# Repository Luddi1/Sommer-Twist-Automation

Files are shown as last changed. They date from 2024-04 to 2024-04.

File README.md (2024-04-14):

# Sommer Twist Automation
 Add-On PCB and ESPHome software to read gate state of Sommer twist 200 (and similar) to implement open and close commands

**Problem**:  Sommer Twist 200 (and similar) gate controllers only have an impulse-input. When toggling this input an open gate closes, closed gate opens and a moving gate stops. 
However, to integrate this into a smarter setup, distinct commands for _open_ and _close_ are needed. 

**Solution**: We read out the LEDs on the gate controller PCB which indicate whether the gate opens or closes, save the state and toggle the impulse-input, depending on the current state and the desired command. 

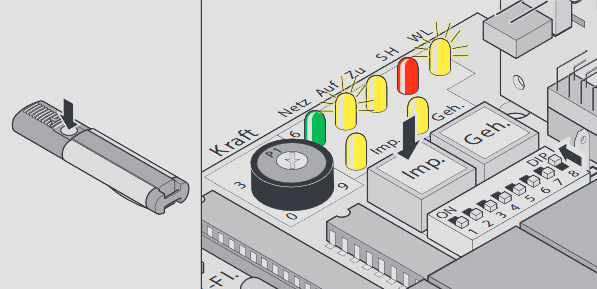
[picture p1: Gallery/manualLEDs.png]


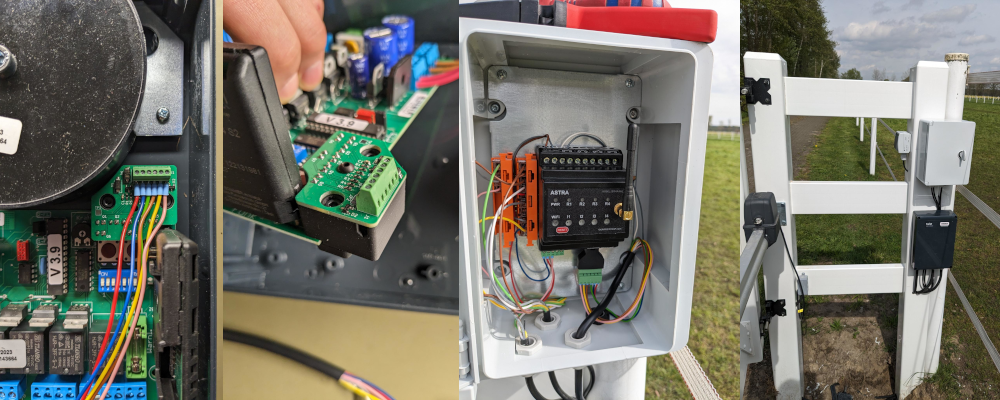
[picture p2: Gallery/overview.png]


This solution needs no hardware hacks on the original Sommer controller. 
Find below the contents of the repository, BOMs for the read-out PCB and the overall system. 

## Contents of repository
* **SommerAdapter** KiCad Project of PCB. Basically implements opto-couplers using the LEDs on the Sommer gate controller. 
* **SommerAdapter-Mount** Fusion 360 Project and step files to mount PCB on Sommer controller. 
* **Setup** ESPHome YAML Script for ASTRA controller and wiring diagram. 
* **Gallery** Some pictures of the installation. 

## BOM SommerAdapter PCB Assembly

Parts for one PCB of SommerAdapter/SommerAdapter.kicad_pcb

Component Refs | Value      | Package | Qty | Reichelt #
-------------- | ---------- | ------- | :-: | ------------
C1 |	100n |	C_0603_1608Metric |	1 | KEM Y5V0603 100N 
R1, R2, R3, R4, R5, R6, R7 |	47k |	R_0603_1608Metric |	7 | SMD-0603 47K
D2, D7 |	PESD3V3S2UT | 	SOT-23 |	2 | PESD3V3S2UT 
D1 |	SS 16 |	D_SMA |	1 | SS 16 
D6 |	P4SMAJ5.0CA |	D_SMA |	1 | P4SMAJ5.0CA 
Q1, Q2, Q3, Q4, Q5, Q6, Q7 |	SFH309-5 |	LED_D3.0mm_Clear |	7 | SFH 309-5 OSO 
J1 |	DG308 | 2,54-6 | 1 | DG308 2,54-6 

## BOM Complete Setup

For presented setup to control a Twist 200. Of course you can make use of the PCB with some other microcontroller and software in your own setup. 

Component | Qty
-------------- | ---------- 
SommerAdapter PCB Assembly |	1
3D printed SommerAdapter-Mount/LowerPart.step  |	1
3D printed SommerAdapter-Mount/UpperPart.step  |	1
ASTRA controller, 4 Relays 16A, 4 AC Input, AC power, LED (BR4A4AL)  |	1
RJ12 6P6C adapter with screw terminals |	1
Panhead screw M3 x 10 |	1
Socket head screw M3 x 16 | 2
Lapp 1030243 LiYY PVC Control Cable 8 x 0.34 mm² |	~2m
Distribiution box 180x240x130mm IP65 F-ELEKTRO 5901087041915 |	1
Momentary switch Aquant 1207-65 IP65 |	1
DIN rail, mounting hardware, some Wago 221 and DIN rail adapter 221-500, 0.34 ferrules  | 

Some notes:
* The printed parts are designed for ABS. Other materials will probably work, too. 
* Keep the cable run for the SommerAdapter PCB as short as possible and avoid runs next to other cables. 
* Flash ESPHome to ASTRA controller and set to SPI mode. See [manual](https://templates.blakadder.com/assets/ASTRA_controller.pdf). Use SPI (left) RJ12 socket. We need the GPIOs and GND/3.3V to power our board.

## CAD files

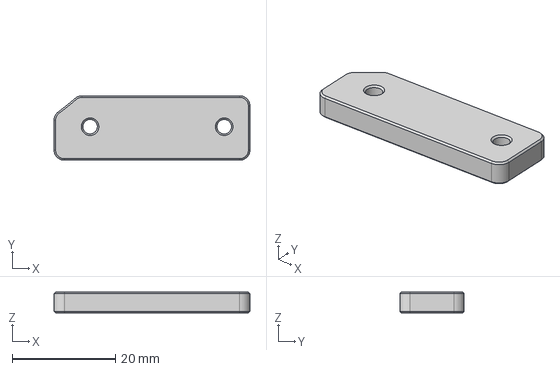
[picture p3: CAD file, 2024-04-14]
SommerAdapter-Mount/LowerPart.step
38.0 x 12.5 x 4.00 mm

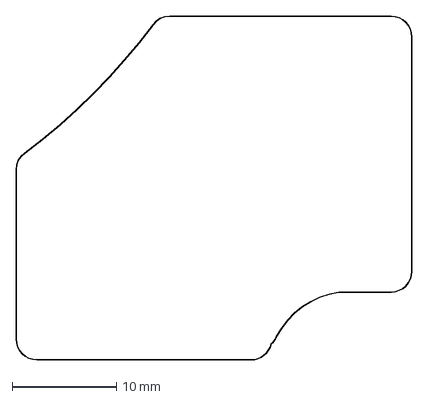
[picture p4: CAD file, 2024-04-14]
SommerAdapter/outline.dxf
38.0 x 33.0 mm

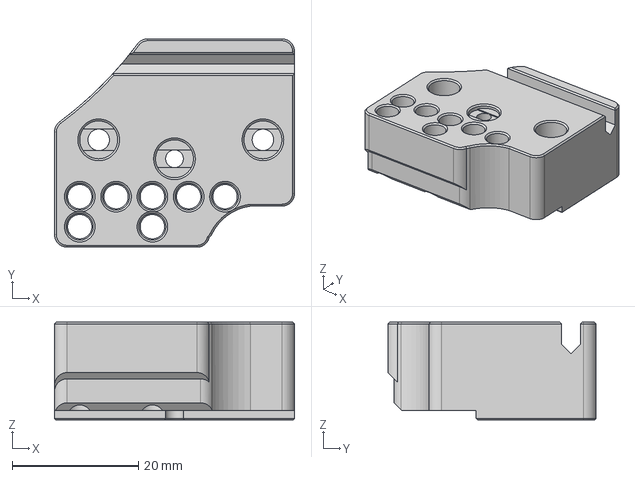
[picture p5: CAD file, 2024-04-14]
SommerAdapter-Mount/UpperPart.step
38.0 x 33.0 x 15.5 mm

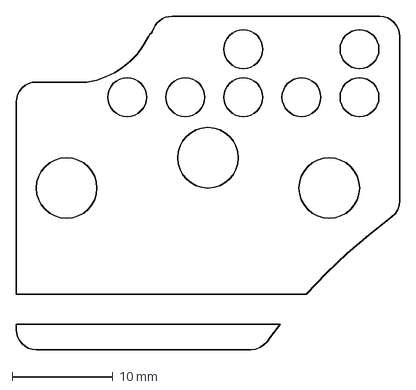
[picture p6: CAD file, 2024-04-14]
SommerAdapter/allfeatures.dxf
38.0 x 33.0 mm

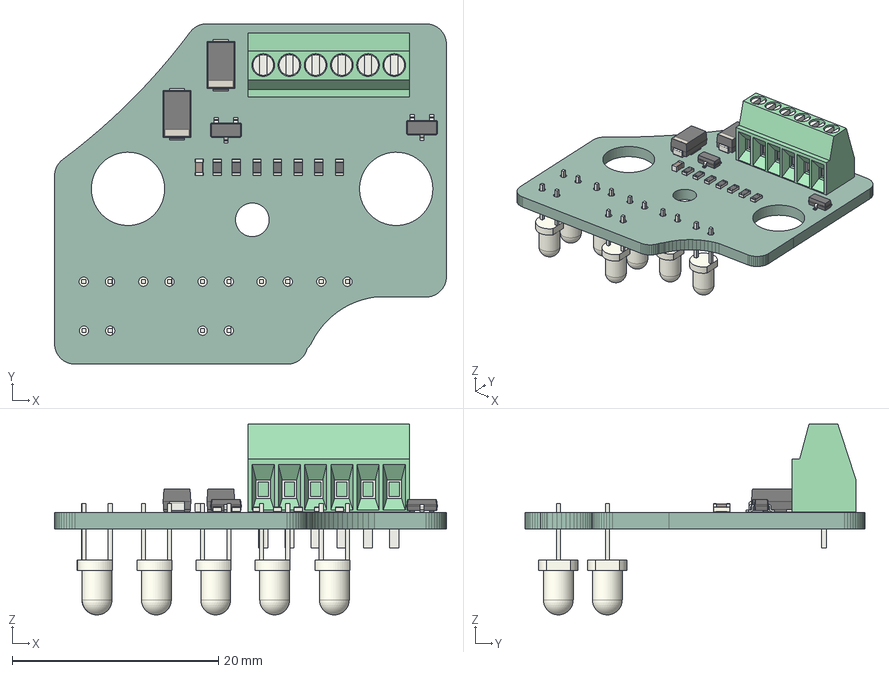
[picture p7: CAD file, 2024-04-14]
SommerAdapter/SommerAdapter.step
38.0 x 33.0 x 18.5 mm
C_0603_1608Metric
R_0603_1608Metric x 7
D_SMA x 2
SOT_23 x 2
TerminalBlock_Phoenix_MPT_05_6_254_1x06_P254mm_Horizontal
LED_D3.0mm_Clear x 7
SommerAdapter PCB

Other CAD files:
SommerAdapter-Mount/SommerAdapter-Mount.f3z

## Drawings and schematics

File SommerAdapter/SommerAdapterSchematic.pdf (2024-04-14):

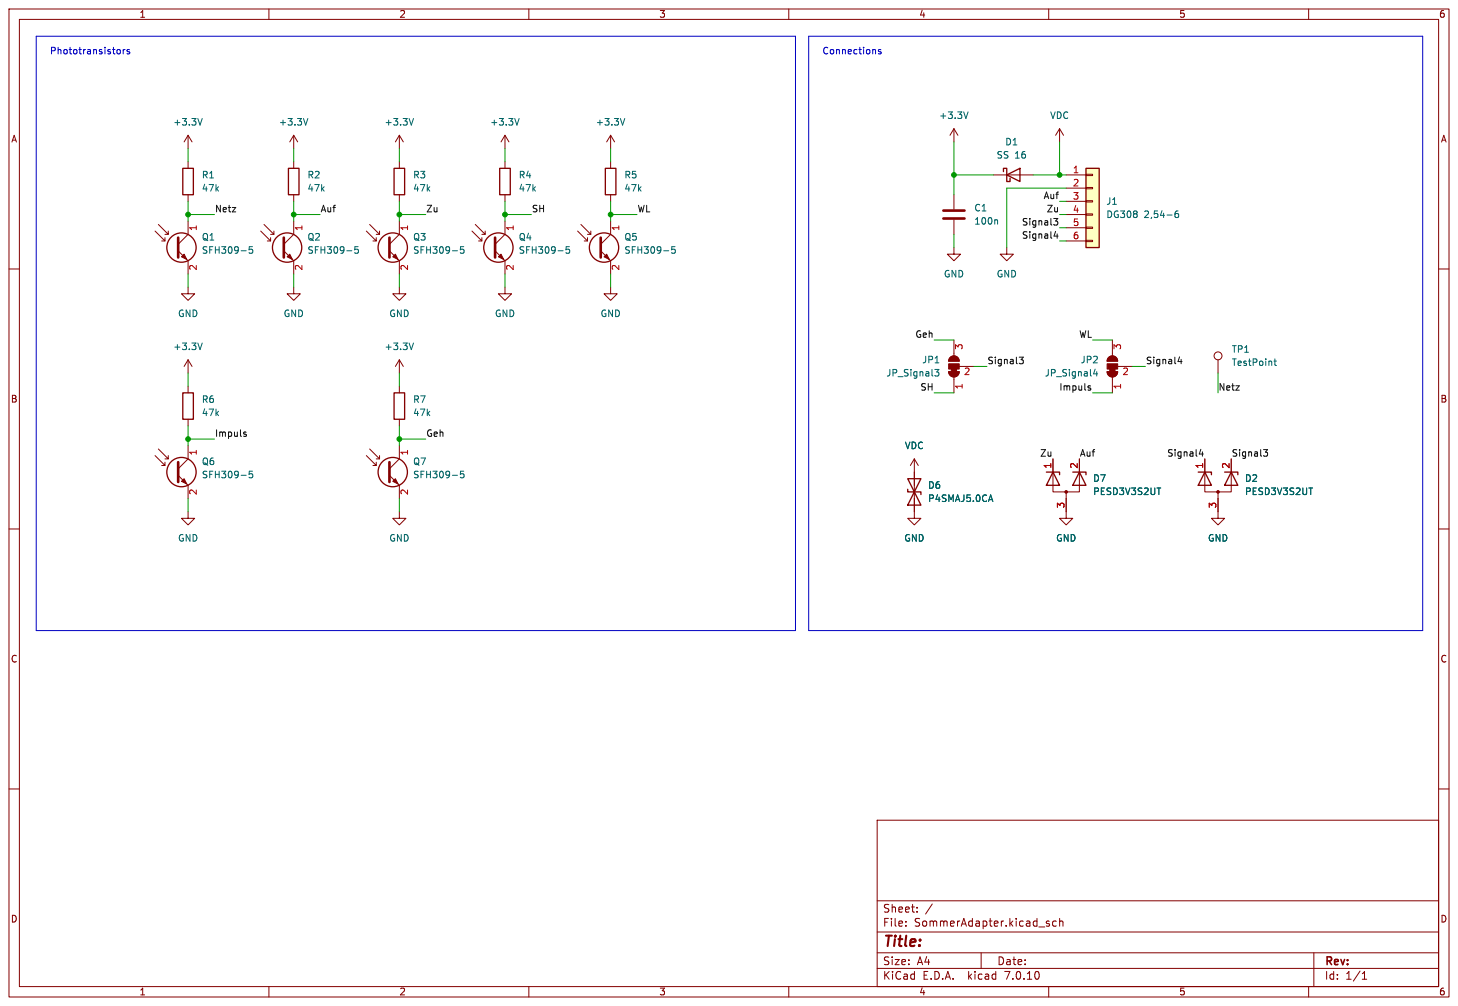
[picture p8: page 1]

Id: 1/1 Title: File: SommerAdapter.kicad_sch Sheet: / GND

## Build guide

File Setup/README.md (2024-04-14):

### Wiring diagram
of SommerAdapter only
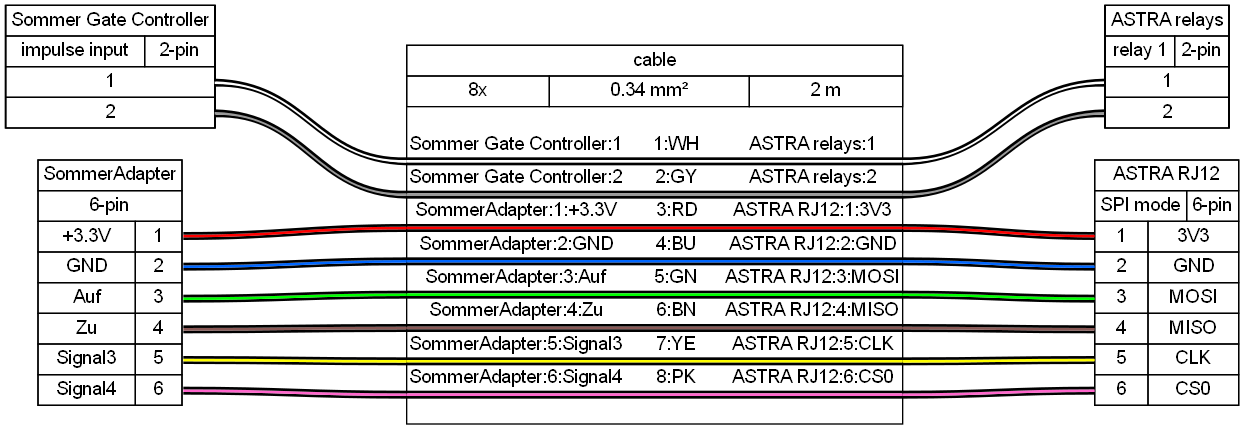
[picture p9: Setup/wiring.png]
Wiring diagram


In the presented setup ASTRA AC input 1 is connected to an induction looop, which triggers when a vehicle approaches. AC input 2 is connected to a momentary switch positioned at the gate. 

### ESPHome setup
ESPhome YAML file: astra-gate.yaml

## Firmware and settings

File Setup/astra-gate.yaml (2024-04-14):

esphome:
  name: astra-gate
  friendly_name: ASTRA-gate
  on_boot:
  # buzzeron on startup
    priority: -100
    then:
      - rtttl.play: 'BarbieGirl:d=4,o=5,b=125:8g#,8e,8g#,8c#6,a'

esp32:
  board: esp32dev
  framework:
    type: arduino

# Enable logging
logger:

ota:
  password: "4231c5ddbc304e2fb4416c7ab1234567"

wifi:
  ssid: !secret wifi_ssid
  password: !secret wifi_password
  reboot_timeout: 15min

  # Enable fallback hotspot (captive portal) in case wifi connection fails
  ap:
    ssid: "Astra-Gate Fallback Hotspot"
    password: "dYCe31234567"

captive_portal:
    
mqtt:
  broker: tower
  topic_prefix: "leusmann/gate"
  reboot_timeout: 15min
  on_message:
    - topic: leusmann/gate
      qos: 0
      then: # logic to open or close depending on current state
        - if:
            condition:
              and:
                - lambda: 'return x == "open";'
                - state_machine.state: "CLOSED"
            then:
              - logger.log: "mqtt -> Is closed, opening"
              - script.execute: open_close_script
        - if:
            condition:
              and:
                - lambda: 'return x == "open";'
                - state_machine.state: "CLOSING"
            then:
              - logger.log: "mqtt -> Is closing, stopping and opening"
              - script.execute: stop_reverse_script
        - if:
            condition:
              and:
                - lambda: 'return x == "close";'
                - state_machine.state: "OPEN"
            then:
              - logger.log: "mqtt -> Is open, closing"
              - script.execute: open_close_script
        - if:
            condition:
              and:
                - lambda: 'return x == "close";'
                - state_machine.state: "OPENING"
            then:
              - logger.log: "mqtt -> Is opening, stopping and closing"
              - script.execute: stop_reverse_script

external_components:
  - source:
      type: git
      url: https://github.com/muxa/esphome-state-machine

status_led:
  pin:
    number: GPIO4
    inverted: true

rtttl:
  output: rtttl_out

# Scripts for actions
script:
  - id: open_close_script
    then:
      - logger.log: "Running open_close_script"
      - output.turn_on: relay1
      - delay: 0.5s
      - output.turn_off: relay1
  - id: stop_reverse_script
    then:
      - logger.log: "Running stop_reverse_script"
      - output.turn_on: relay1
      - delay: 0.5s
      - output.turn_off: relay1
      - delay: 3.0s
      - output.turn_on: relay1
      - delay: 0.5s
      - output.turn_off: relay1

output:
  - platform: ledc
    pin: GPIO12
    id: rtttl_out
  - platform: gpio
    pin: 25
    id: relay1 # triggering gate controller
  - platform: gpio
    pin: 26
    id: relay2 # unused
  - platform: gpio
    pin: 33
    id: relay3 # unused
  - platform: gpio
    pin: 32
    id: relay4 # unused

binary_sensor:
  - platform: gpio
    name: "SWITCH 1" # signal from dual induction loop, triggered only when vehicle approaching
    pin: 
      number: 34
      inverted: true
      mode:
        input: true
    on_press: 
      if:
        condition:
          state_machine.state: "CLOSED"
        then:
          - logger.log: "Induction loop triggered -> Is closed, opening"
          - script.execute: open_close_script
        else:
          if:
            condition:
              state_machine.state: "CLOSING"
            then:
              - logger.log: "Induction loop triggered -> Is closing, stopping and opening"
              - script.execute: stop_reverse_script

  - platform: gpio
    name: "SWITCH 2" # manual switch, located at gate
    pin: 
      number: 35
      inverted: true
      mode:
        input: true
    on_press: 
      then:
        - logger.log: "Manual switch pressed -> toggle gate"
        - output.turn_on: relay1
        - delay: 0.5s
        - output.turn_off: relay1

  - platform: gpio
    name: "SWITCH 3"
    pin: 
      number: 36
      inverted: true
      mode:
        input: true

  - platform: gpio
    name: "SWITCH 4"
    pin: 
      number: 39
      inverted: true
      mode:
        input: true

  - platform: gpio
    name: "Impuls"
    pin: 
      number: 5
      inverted: true
      mode:
        input: true
    filters:
      - delayed_on: 100ms
      - delayed_off: 100ms

  - platform: gpio
    name: "SH"
    pin: 
      number: 18
      inverted: true
      mode:
        input: true
    filters:
      - delayed_on: 100ms
      - delayed_off: 100ms

  - platform: gpio
    name: "Zu"
    pin: 
      number: 19
      inverted: true
      mode:
        input: true
    filters:
      - delayed_on: 100ms
      - delayed_off: 100ms
    on_press:
      state_machine.transition: ZuON
    on_release: 
      state_machine.transition: ZuOFF
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

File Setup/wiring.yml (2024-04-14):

connectors:
  SommerAdapter:
    pinlabels: [+3.3V, GND, Auf, Zu, Signal3, Signal4]
  Sommer Gate Controller:
    pincount: 2
    type: impulse input
  ASTRA relays:
    pincount: 2
    type: relay 1 
  ASTRA RJ12:
    pinlabels: [3V3, GND, MOSI, MISO, CLK, CS0]
    type: SPI mode

cables:
  cable:
    gauge: 0.34 mm2
    length: 2
    colors: [WH, GY, RD, BU, GN, BN, YE, PK]
    shield: false

connections:
  -
    - Sommer Gate Controller: [1,2]
    - cable: [1,2]
    - ASTRA relays: [1,2]
  -
    - SommerAdapter: [1-6]
    - cable: [3-8]
    - ASTRA RJ12: [1-6]
  

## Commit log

2024-04-14 Added all source files
    Added all source files and description in readme
    [LowerPart.step, SommerAdapter-Mount.f3z, SommerAdapter.kicad_pcb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]
2024-04-14 Added wiring diagram
